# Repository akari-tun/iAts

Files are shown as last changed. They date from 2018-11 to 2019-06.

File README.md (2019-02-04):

# iAts
A antenna tracker system for UAV.

## 项目介绍
Arduino自动跟踪云台
蓝牙版AAT

用于装载定向高增益图传天线，通过图传的音频通道传送飞机的坐标位置与高度，再根据本地位置与高度计算出需要指向的方向与俯仰角度，从而将自动将天线指向飞机，不需要人肉调整天线角度，更加专注于飞行与享受FPV的过程。

大部分代码基本来源于开源项目 amv-open360tracker_RX_v1_user 项目地址 https://github.com/raul-ortega/amv-open360tracker/  
修改了以下功能：
1. 修改了程序流程
2. 开发了手机APP进行调参与监控（通过蓝牙连接）
3. 增加了HC05蓝牙模块与手机连接，通过手机APP进行调参
4. 与手机APP通讯，将飞机位置数据通过APP传到手机（使用自定义TLV格式的协议）
5. 手机APP上显示飞机的位置

## APP

[iAts_app](https://github.com/akari-tun/iAts_app) 可以对云台进行调参与跟踪飞机位置。

发布版本：
[release v1.0.0-perview](https://github.com/akari-tun/iAts_app/releases/download/1.0.0-perview/iAts_app_V1.0.0-perview.apk)
## 特点

- 低成本，基于328p芯片运行，可以直接使用[MWC MultiWii SE v2.6](https://s.taobao.com/search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)飞控板，或是使用[Arduino Pro Mini](https://store.arduino.cc/usa/arduino-pro-mini)+[HMC5883模块](https://s.taobao.com/search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)/[QMC5883模块](https://s.taobao.com/search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)+[MPU6050模块](https://s.taobao.com/search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)进行构建。
- 云台的运动使用舵机驱动，水平方向使用360°舵机，俯仰方向使用180°或90°舵机，低成本的舵机可以使用[MG995](https://item.taobao.com/item.htm?spm=a230r.1.14.20.24c52706K8ff73&id=45136514387&ns=1&abbucket=11#detail)，它有360°版本与180°版本。
- [OLED](https://item.taobao.com/item.htm?spm=a1z10.5-c-s.w4002-15846751795.28.57594e5cFUP7UZ&id=524527857468)屏幕显示数据，可以显示飞机坐标，速度，GPS星数，本地位置，方向等数据。
- 开发了手机APP进行调参与监控，可以在APP的地图中显示飞机的位置。
- 发射端可以支持NMEA协议与MAVLink协议，输出标准的LTM协议与地面端通信。
- 使用图传的音频通道传输数据到地面端，地面端与发射端都使用[TCM3105芯片](https://s.taobao.com/search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)进行数模转换。
- 云台旋转部分与底座需要使用[微型滑环](https://s.taobao.com/search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)，防止绕线。
- 使用卡尔曼滤波算法融合加速度计与指南针数据，减少指南针漂移引起的抖动。
- 地面端使用了MOZ8上djzoom大佬设计的PCB，原帖：[让每个人都能用起的舵机版AAT](http://www.moz8.com/forum.php?mod=viewthread&tid=83868&highlight=%E8%88%B5%E6%9C%BA%2BAAT&_dsign=e2235060)
- 发射端让同事帮忙画了新的PCB。
- AAT通过蓝牙连接手机，通过手机获取本地GPS位置，省略了“设置家”的步骤或是“本地GPS模块”。
  
## 成品展示

#### 硬件电路部

##### 接收端原理图
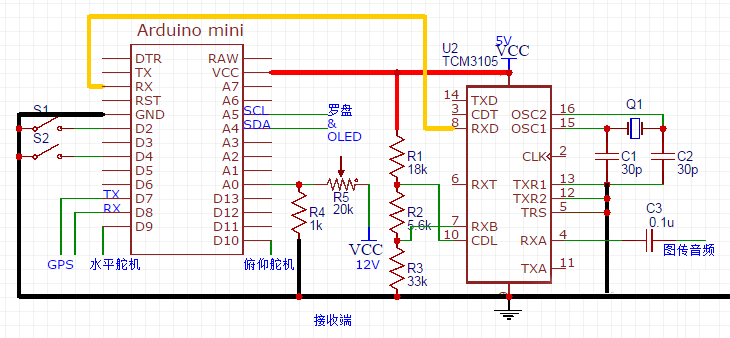
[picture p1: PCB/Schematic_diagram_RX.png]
Schematic_diagram_RX

  
##### 发射端原理图
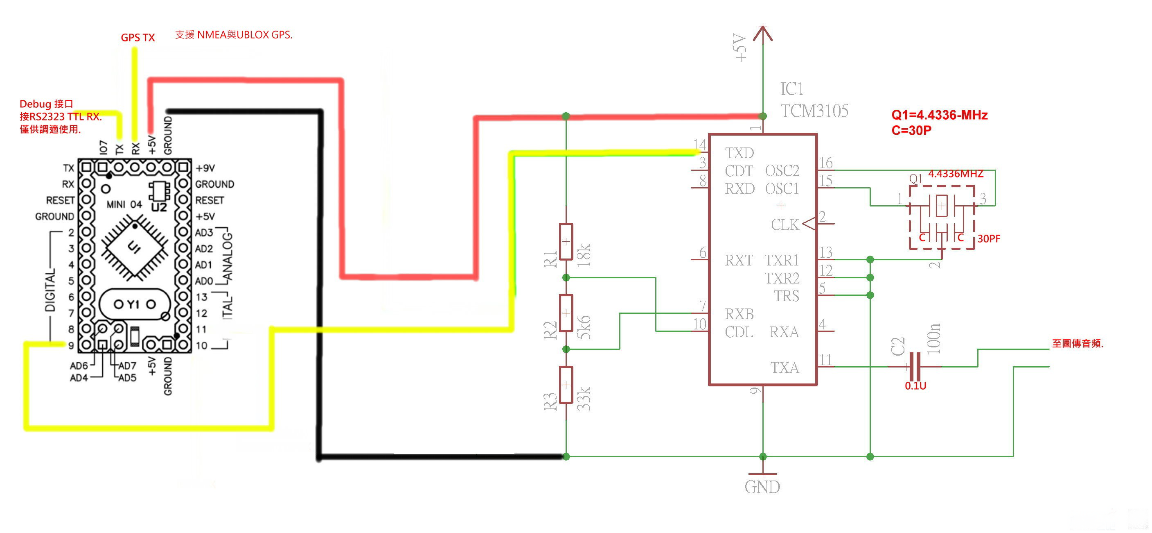
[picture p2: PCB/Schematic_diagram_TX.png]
Schematic_diagram_TX

  
##### 打样回来的PCB
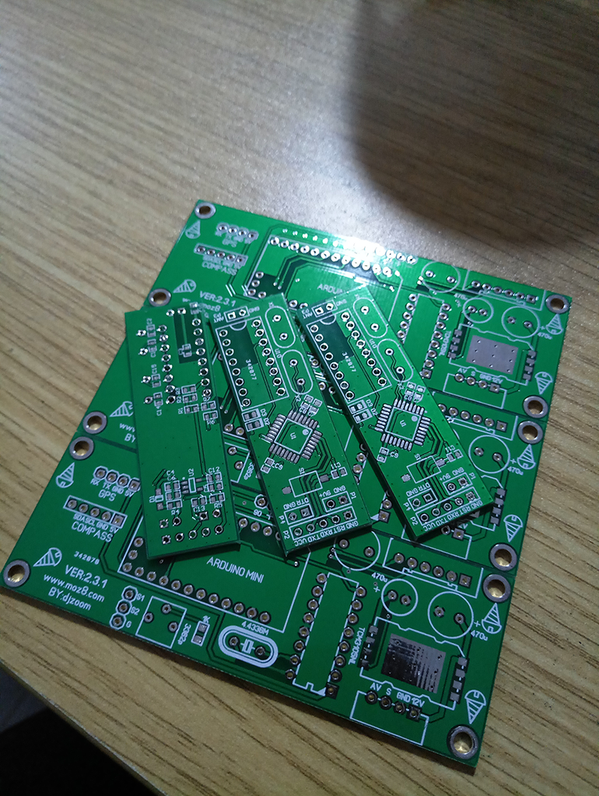
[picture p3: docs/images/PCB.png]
PCB

  
##### 发射机
焊好的发射端，由于使用5V供电，所以电源部分可以不需要焊了

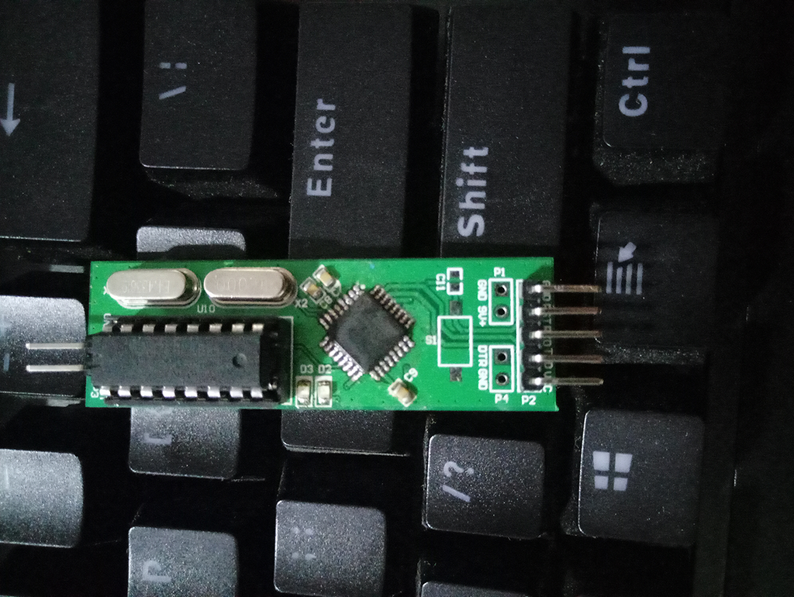
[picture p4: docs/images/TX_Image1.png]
TX


#### 前面板

前面板包含以下几个部分：
- 3个LED灯
  红色接收到图传信号并解析成功数据开始闪烁，蓝色在手机蓝牙连接成功并向手机发送数据闪烁，绿色在接收到手机发送的数据闪烁。
- 12V电源插口
  用于给图传接收机供电。
- AUX音视频插口 
  用于连接图传接收机，传输视频与音频信号，视频信号通过滑环穿过底座接显示屏，音频信号通过TCM3105芯片转换为数字信号。
- OLED屏幕
  显示GPS坐标，速度，方向，云台指向，云台电压，本地GPS坐标，高度等数据。
  
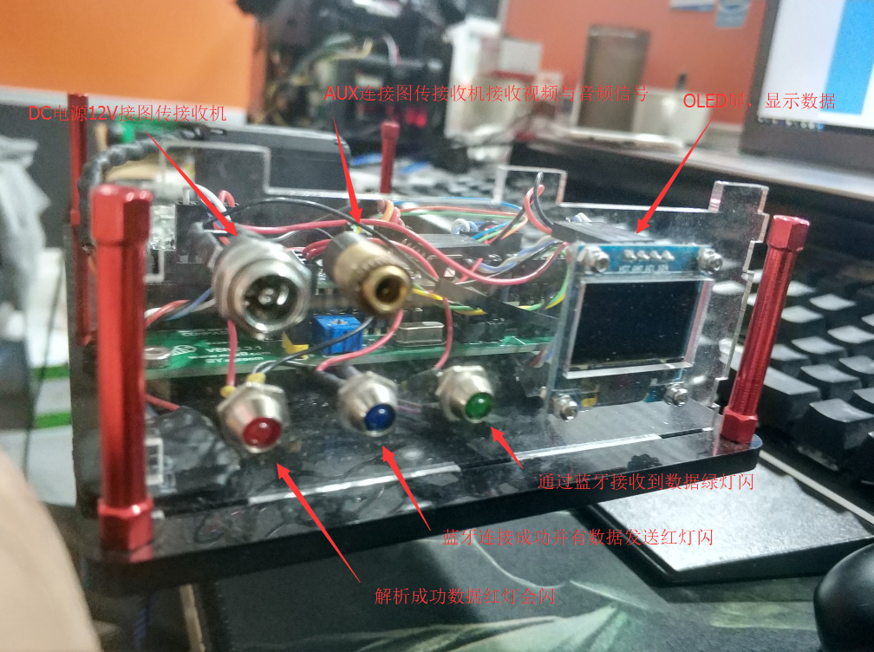
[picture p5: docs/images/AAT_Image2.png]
 

#### 内部细节

##### MPU6050模块
MPU6050用于测量水平旋转的加速度，使用卡尔曼滤波算法融合测量的指南针数据进行计算，消除指南针数据的漂移。

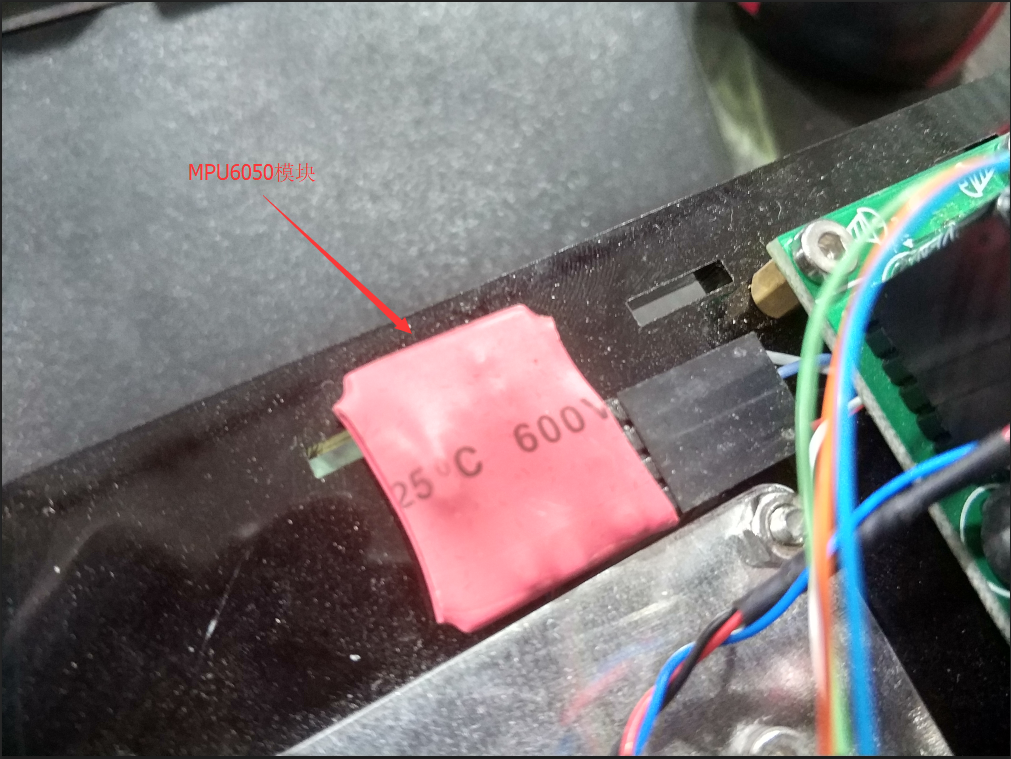
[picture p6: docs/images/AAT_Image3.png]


##### HMC5883L模块
HMC5883L磁力计用于测量指向的角度，通过融合MPU6050的加速度数据进行卡尔曼滤波来消除漂移。

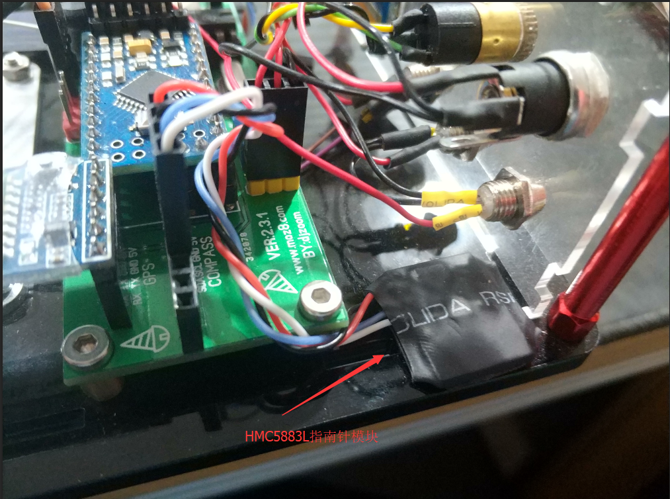
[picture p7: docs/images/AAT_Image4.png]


##### 微型滑环
平台与底座使用滑环导电，通过滑环可以防止360°旋转的时候将导线缠绕。

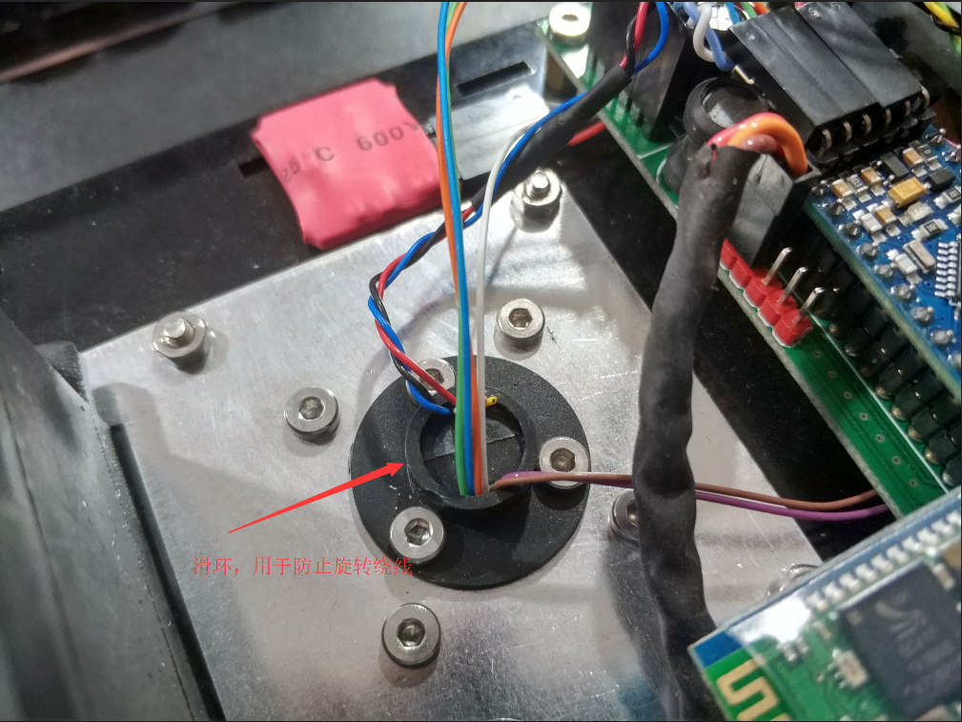
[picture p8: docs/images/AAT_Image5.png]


##### HC05蓝牙模块
蓝牙模块用于与手机蓝牙连接

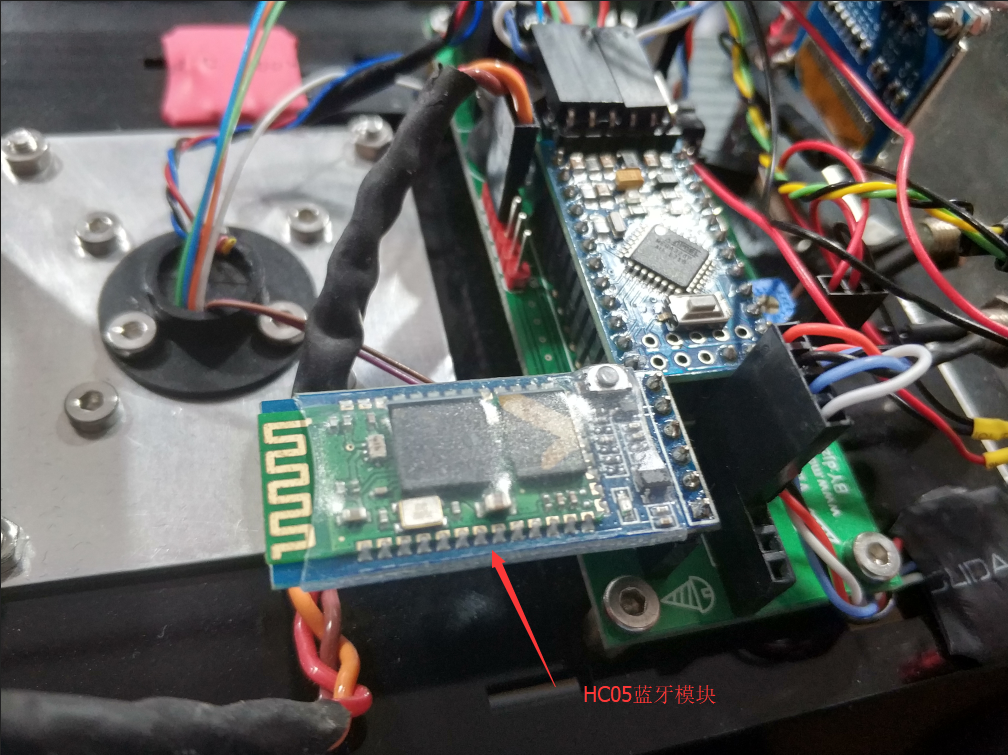
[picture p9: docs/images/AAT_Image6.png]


##### 接收板
接收板上焊接了Arduino Pro Mini模块，开关电源模块，TCM3105芯片，供电分做量部分，通过滑环进来的12V电源，一部分通过开关电源模块降压到5V给两个舵机供电，好处是支持电流大，效率高，但是纹波比较大，所以后部有滤波电容，另一部分通过LM7805电源芯片降压到5V给Pro Mini供电。

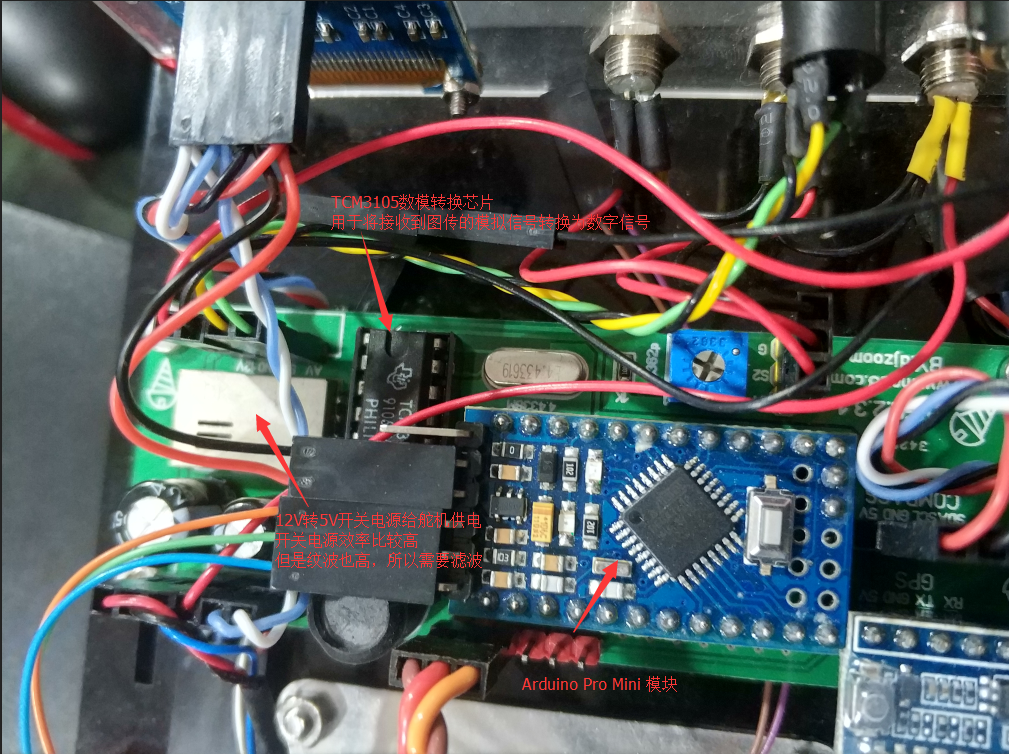
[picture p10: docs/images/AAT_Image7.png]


##### 水平360°舵机
水平舵机提供360°的旋转支持。

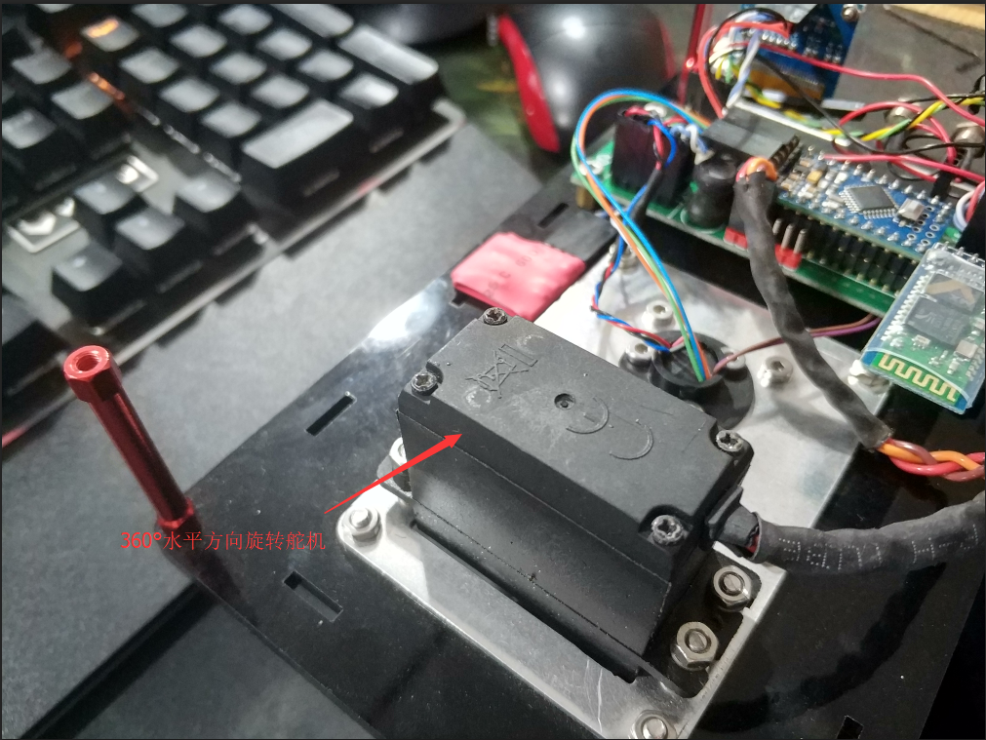
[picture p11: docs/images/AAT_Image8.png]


##### 内部整体图

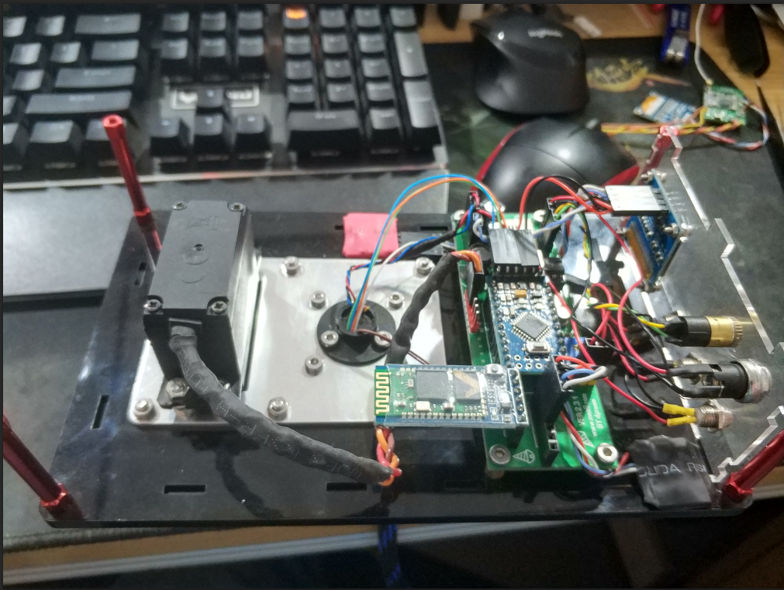
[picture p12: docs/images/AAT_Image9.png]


#### 外部细节

##### 底座
底座机械部分由djzoom群里的大佬设计加工，我购买的成品，底座上的齿轮固定，通过水平舵机上的齿轮旋转带动云台水平转动，底座内有两个轴承支撑平台，滑环的线通过轴承中心穿出底座，由于底座使用了CNC加工，虽然坚固漂亮，但是成本较高。

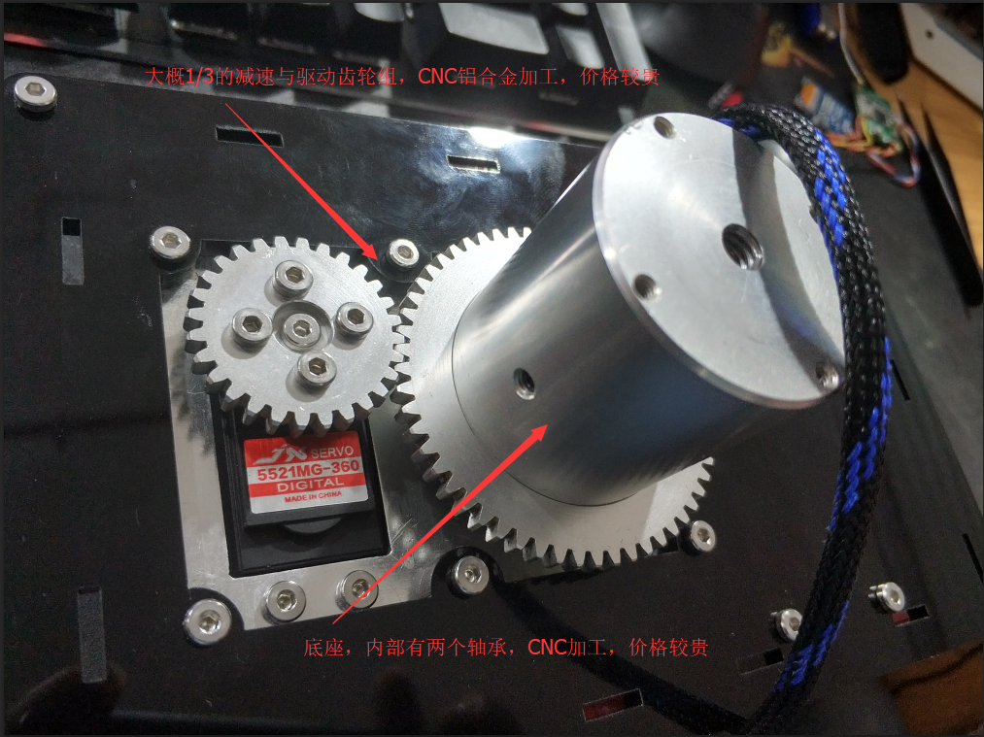
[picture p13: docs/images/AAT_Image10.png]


##### 1/4英寸螺孔
底部提供了标准的1/4英寸螺孔，可以直接安装到普通的相机三脚架上。

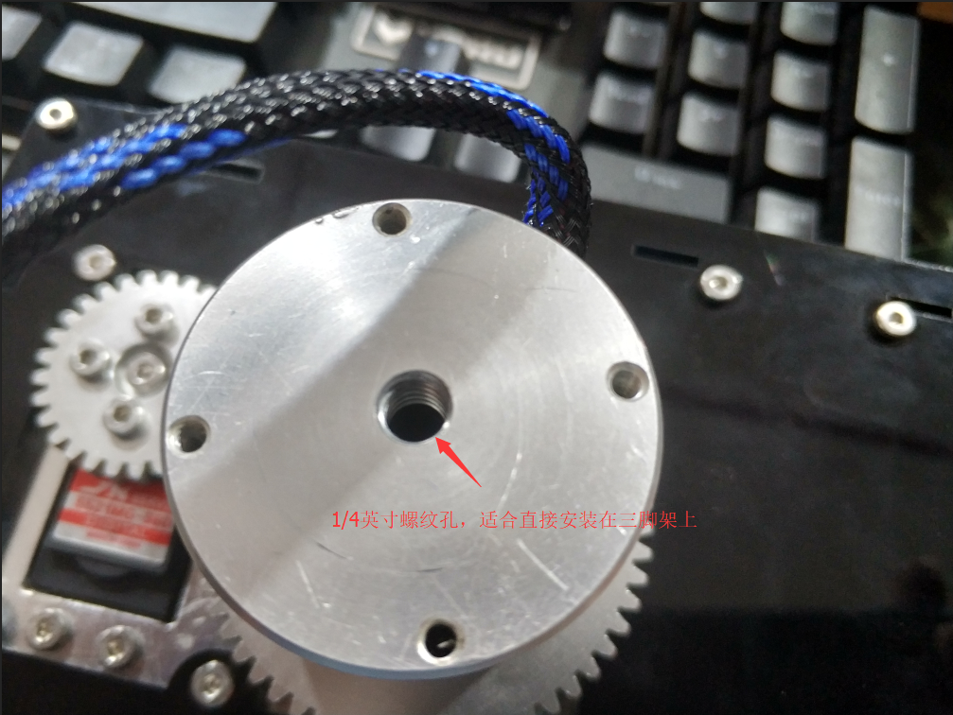
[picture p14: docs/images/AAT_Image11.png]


##### 外部整体图
外壳使用了5mm黑色亚克力加工了上盖板与下盖板，上下盖板间使用了40mm铝柱支撑固定,俯仰固定安装在上盖板上，使用了舵机配送的摇臂来安装天线支架，天线支架使用1/4英寸手拧螺丝来安装[枫叶23db大平板](https://item.taobao.com/item.htm?spm=a1z10.5-c.w4002-10110629054.23.3cf95b54f4w6pb&id=543939433629)，图传接收机使用了开源的双接收，用3D打印的外壳，直接用双面胶粘在盖板上，另外把水平尺也装在了盖板上，用于使用时调平。

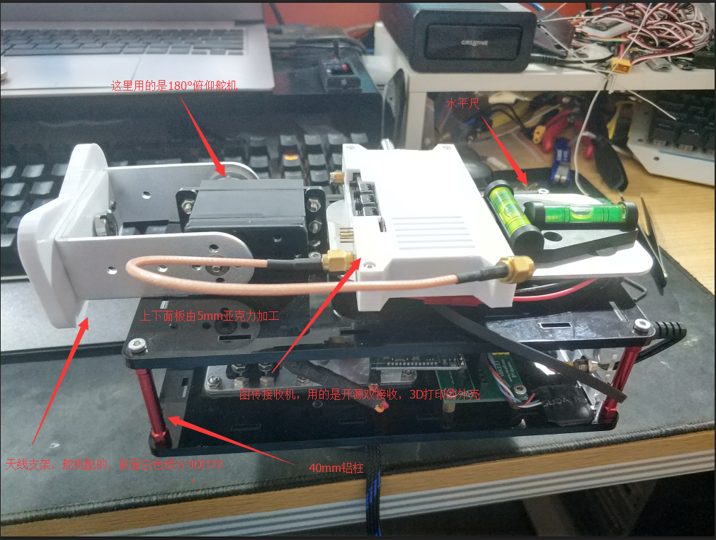
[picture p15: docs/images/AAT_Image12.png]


#### 外场使用

##### 整体图
正在测试的成品，用的是枫叶大平板，由于比较重，有点抖。

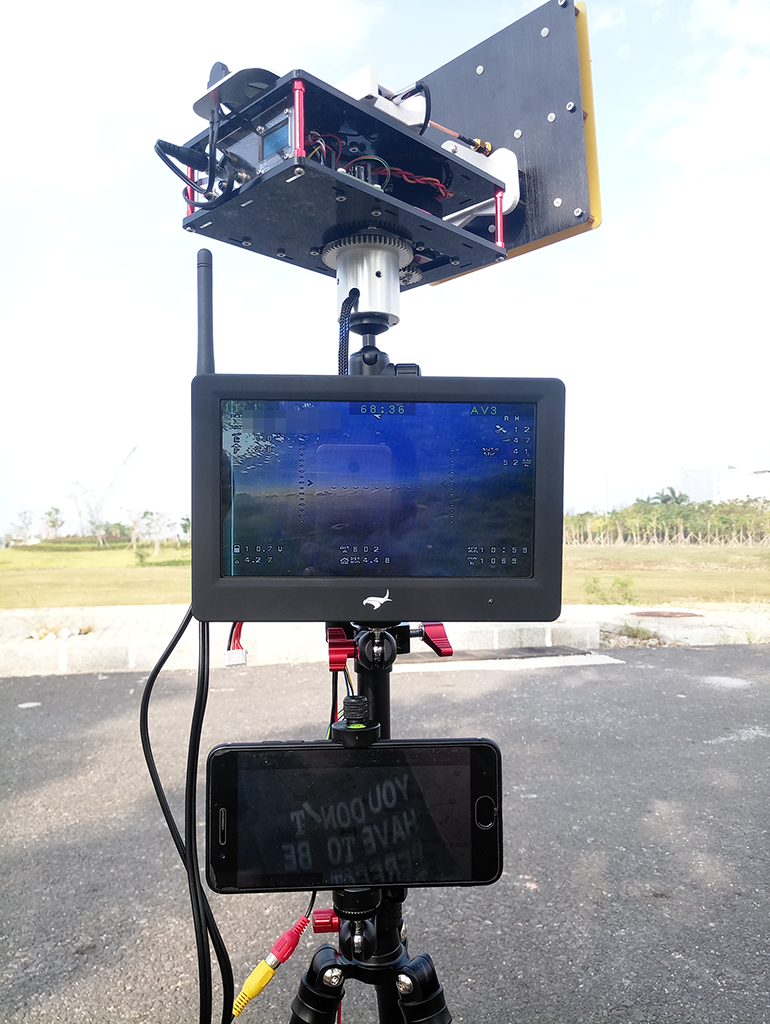
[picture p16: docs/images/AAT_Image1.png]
成品


##### APP截图
APP跟踪界面截图，可以看到飞机位置，经纬度，高度，距离，速度，AAT的电压，指向角度，俯仰角度

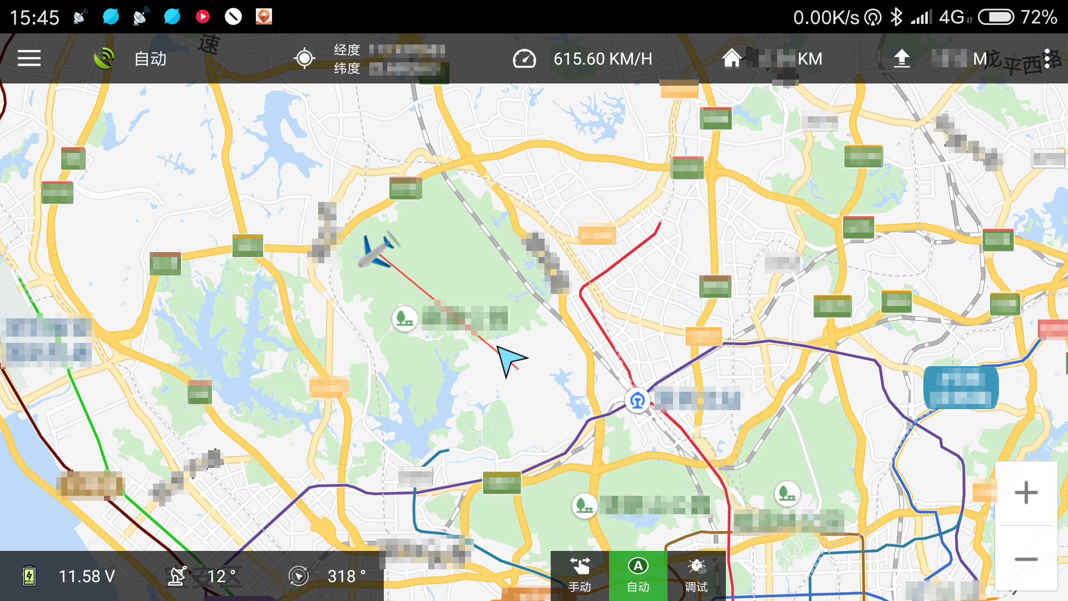
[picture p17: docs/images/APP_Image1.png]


调参界面
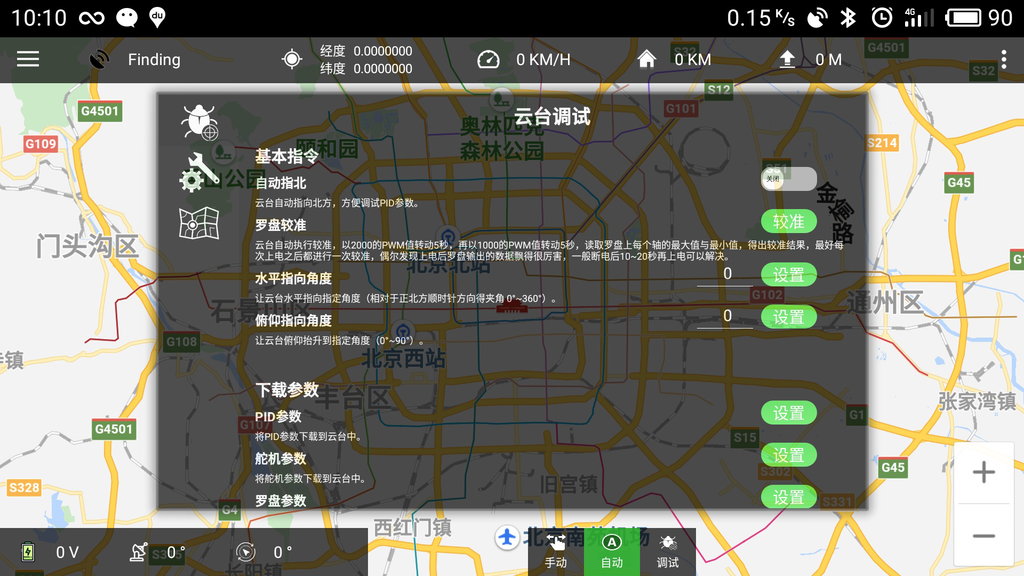
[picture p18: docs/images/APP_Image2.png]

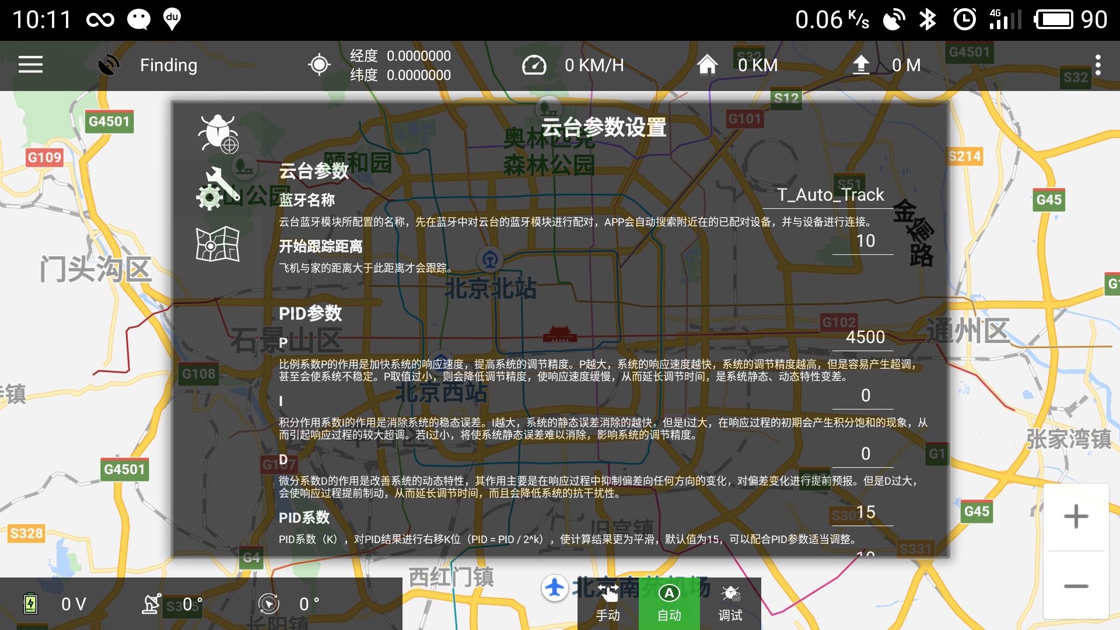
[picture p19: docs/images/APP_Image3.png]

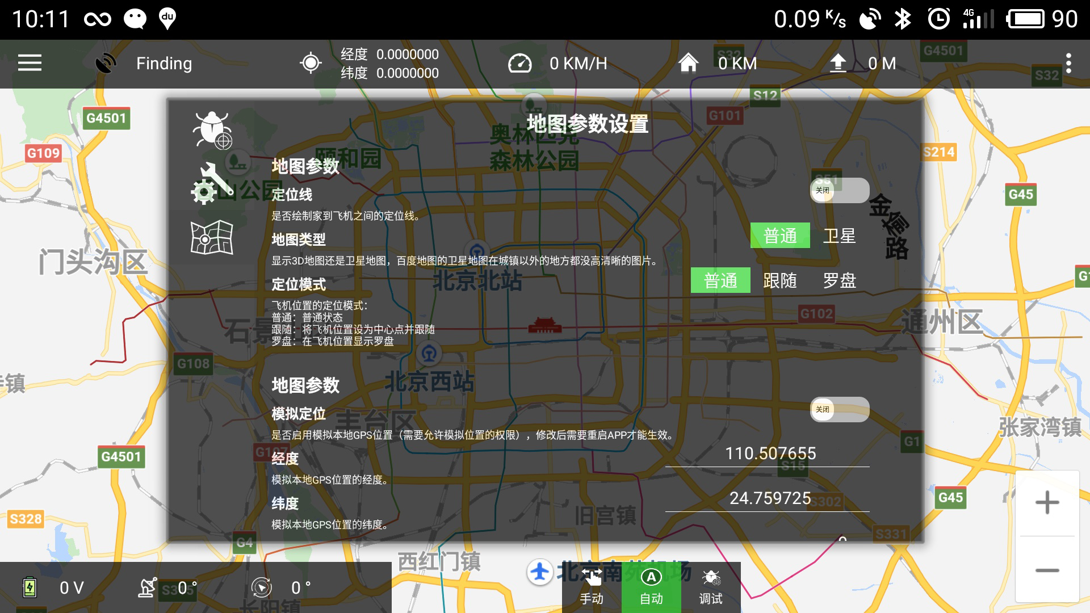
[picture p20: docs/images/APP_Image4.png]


#### 视频：<Br/>
- [模拟测试](https://www.bilibili.com/video/av31897946/) <Br/>
- [上飞机实测](https://www.bilibili.com/video/av33431415/)

## 安装教程

正在撰写。。。

## 使用说明

正在撰写。。。

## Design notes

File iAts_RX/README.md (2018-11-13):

# T_Auto_Tracker

#### 项目介绍
Arduino自动跟踪云台
蓝牙版AAT

#### 软件架构
大部分代码基本来源于开源项目 amv-open360tracker_RX_v1_user 项目地址 https://github.com/raul-ortega/amv-open360tracker/  

修改了以下功能：
1. 重写了loop()函数
1. 蓝牙调参，蓝牙上传数 
2. 蓝牙传输GPS数据，在手机上显示飞机位置  
3. 修改了一点点发射端与接收端的通讯协议，传输了更多的数据  
4. 优化PID算法，加入变积分过程  
5. 加入国产QMC5883芯片的支持  
6. 加入MPU6050并使用卡尔曼滤波，消除指南针漂移
  
针对此固件的APP正在开发中。。。

#### 安装教程

1. xxxx
2. xxxx
3. xxxx

#### 使用说明

1. xxxx
2. xxxx
3. xxxx

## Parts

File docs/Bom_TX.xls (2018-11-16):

BOM
类型 | Comment | 数量 | 位号 | 封装
IC | TCM3105 | 1 | U1 | DIP16
 | ME6219 | 1 | U2 | LC-SOT-23-5
 | ATmaga328P-AU | 1 | U1 | TQFP80P900X900X120_HS-32N
电容 | 30pF/0603/5% | 4 | C1, C2,C14,C15 | C0603
 | 0.1uF/50V/10% | 7 | C3, C4, C7, C8, C9, C10, C13 | C0603
 | 2.2uF/50V/10% | 2 | C5, C11 | C0603
 | 10uF/10V/10%钽电容 | 2 | C6, C12 | A型
电阻 | 100R/5%/0603 | 3 | R4, R6, R7 | R0603
 | 5K6/5%/0603 | 1 | R2 | R0603
 | 10K/5%/0603 | 1 | R5 | R0603
 | 18K/5%/0603 | 1 | R1 | R0603
 | 33K/5%/0603 | 1 | R3 | R0603
晶振 | 4.4336MHz | 1 | X1 | LC-HC-49S
 | 12Mhz | 1 | X2 | LC-HC-49S
二极管、LED | 1N4148 | 1 | D1 | SOD123
 | 蓝色LED | 1 | D2 | D0603
 | 红色LED | 1 | D3 | D0603
排针 | 2pin2.54mm间距排针 | 2 | P1, P3 | HDR1X2
 | 5pin2.54mm间距排针 | 1 | P2 | HDR1X5
按键 | SW-PB | 1 | S1 | Buttle_SMD

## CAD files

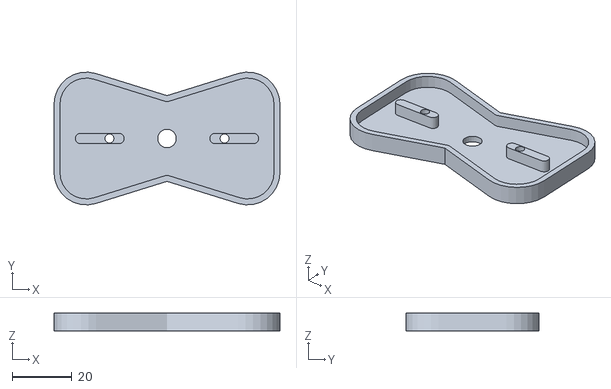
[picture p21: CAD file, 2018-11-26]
docs/cases/Antenna_Holder_2.stl
75.6 x 44.4 x 6.00

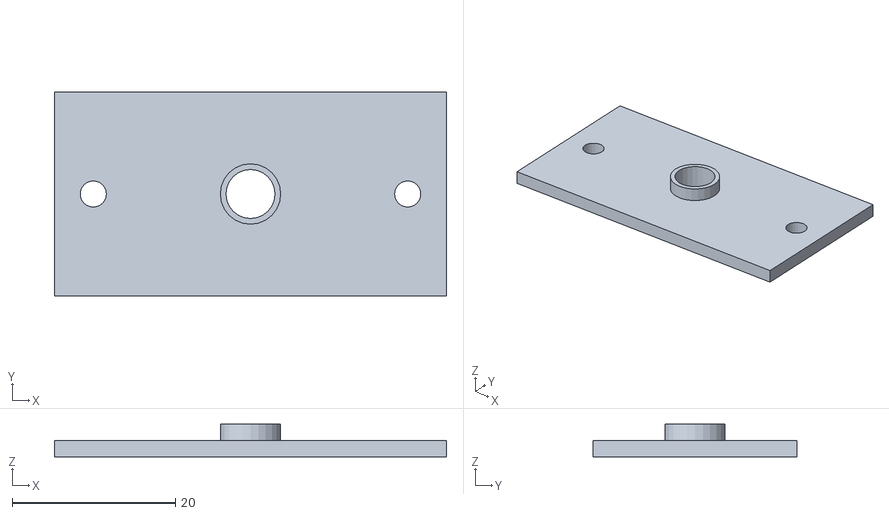
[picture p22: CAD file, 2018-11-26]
docs/cases/Antenna_Holder_1.stl
48.0 x 25.0 x 4.00

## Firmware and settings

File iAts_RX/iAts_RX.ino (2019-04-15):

/*
作者：TanJun
用途：蓝牙版AAT

部分代码来源于开源项目 amv-open360tracker_RX_v1_user 项目地址 https://github.com/raul-ortega/amv-open360tracker/
在此基础上做了一些修改
1.重新构建主流程，使执行过程更合理
2.蓝牙调参，蓝牙上传数
3.蓝牙传输GPS数据，在手机上显示飞机位置
4.加入了PID变积分算法，使之能更快的修正误差
*/

#include <Arduino.h>
#include <Wire.h>			  //I2C
#include <SSD1306Ascii.h>	  //OLED屏
#include <SSD1306AsciiWire.h> //OLED屏
#include <SoftwareSerial.h>   //软串口
#include "defines.h"		  //基础定义
#include "config.h"			  //配置定义
#include "telemetry.h"		  //通讯解析
#include "tprotocol.h"		  //协议
#include "battery.h"		  //电压测量
#include "IMU.h"		  	  //惯性测量单元
#include "servos.h"			  //舵机控制
#include "calc.h"			  //计算数据

SoftwareSerial digitalSerial(T_GPS_RX_PIN, T_GPS_TX_PIN);
SSD1306AsciiWire oled;
IMU imu;

char oled_str[24];

struct Airplane airplane;
struct Tracker tracker;
struct Parameter TParam;

long Error[11];
long Accumulator;
long PID;
// double AccGain;
int16_t _servo_tilt_must_move = -1;

int softserial_delay = (int)round(10000000.0f / (DIGITAL_SERIAL_BAUDRATE)); // time to wait between each byte sent.

// uint16_t last_course;
// unsigned long airplane_pos_time;
unsigned long airplane_upload_time;
unsigned long tracker_upload_time;
unsigned long heart_upload_time;
unsigned long compass_time;
unsigned long oled_time;

boolean is_bt_conn;

uint8_t *p_send_data;
uint8_t send_len;
uint8_t send_index;
uint32_t frame_timer;

void getError();
void calculatePID();
boolean sendToBluetooth();
void calcTilt();

void setup()
{
	pinMode(VOLTAGEDIVIDER, INPUT);
	pinMode(LED_DIGITAL_PIN, OUTPUT);
	pinMode(LED_SERIAL_PIN, OUTPUT);
	pinMode(LED_ENCODE_PIN, OUTPUT);
	pinMode(EN_33V_PIN, OUTPUT);

	/* 激活3.3V稳压模块 */
	digitalWrite(EN_33V_PIN, HIGH);
	delay(100);

	/* 初始化一些变量 */
	tracker.mode = 1;
	p_send_data = 0;
	send_len = 0;
	send_index = 0;
	airplane_upload_time = 0;
	tracker_upload_time = 0;
	heart_upload_time = 0;
	compass_time = 0;
	oled_time = 0;
	SERVO_TILT_HAS_ARRIVED = true;
	//AccGain = 0;

	//测试代码初始化
	// tracker.mode = 1;
	// TParam.pid_p = 6000;
	// TParam.pid_i = 50;
	// TParam.pid_d = 200;
	// TParam.pid_divider = 15;
	// TParam.pid_max_error = 40;
	// TParam.tilt_min = 1100;
	// TParam.tilt_max = 2150;
	// TParam.pan_center = 1505;
	// TParam.pan_min_speed = 50;
	// TParam.compass_offset = 180;
	// TParam.compass_declination = 0;
	// TParam.start_tracking_distance = 10;
	/* ------------------------------------------ */

	//设置参考电压为默认值
	analogReference(BATTERYMONITORING_VREF_SOURCE);

	/* OLED屏初始化 */
	Wire.begin();
	oled.begin(&Adafruit128x64, OLED_I2C_ADDRESS);
	oled.set400kHz();
	oled.setFont(font8x8);
	oled.println("T Auto Tracker");
	oled.println("Version 1.0.0");
	oled.println("    ");
	delay(1000);
	/* ------------------------------------------ */

	HAS_ALT = false;
	HAS_FIX = false;
	HOME_SETED = false;
	BT_CONNECTED = false;
	BT_DATA_SENDING = false;

	/* 初始化电子指南针 */
	Wire.setClock(uint32_t(400000L));
	Wire.begin();
	oled.println("IMU Init...");
	imu.init();
	/* ------------------------------------------ */

	/* 初始化传输协议 */
	oled.println("Protocol Init...");
	tprotocol(&airplane, &tracker, &TParam);
	telemetry(&airplane);
	/* ------------------------------------------ */

	/* 初始化传输协议 */
	oled.println("Servos Init...");
	//initServos(&tracker_param);
	initServos(&TParam);
	/* ------------------------------------------ */

	/* 软串口--接收AD转换后的数字信号 */
	digitalSerial.begin(DIGITAL_SERIAL_BAUDRATE);
	/* ------------------------------------------ */

	/* 物理串口--链接蓝牙模块 */
	Serial.begin(PHYSICAL_SERIAL_BAUDRATE);
	/* ------------------------------------------ */

	TParam.pid_divider = 15;
	// airplane_pos_time = millis();
	airplane_upload_time = millis();
	tracker_upload_time = millis() + 500;
	heart_upload_time = millis();
	compass_time = millis();
	oled_time = millis();
}

void loop()
{
	//int8_t i;

	digitalWrite(LED_DIGITAL_PIN, LOW);
	digitalWrite(LED_ENCODE_PIN, LOW);
	digitalWrite(LED_SERIAL_PIN, LOW);

	//if (Serial.available())
	if (digitalSerial.available())
	{
		//uint8_t c = Serial.read();
		uint8_t c = digitalSerial.read();
		//digitalSerial.write(c);

		if (encodeTargetData(c) && HAS_ALT && HAS_FIX) digitalWrite(LED_DIGITAL_PIN, HIGH);

		digitalWrite(LED_DIGITAL_PIN, HIGH);

		// else if (tracker.mode == TRACKER_MODE_DEBUG)
		// {
		// 	//target heading in degree
		// 	if (c == 'H' || c == 'h') tracker.course = Serial.parseInt();
		// 	else if (c == 'T' || c == 't')
		// 	{
		// 		//tilt angle in degree
		// 		int value = Serial.parseInt();
		// 		if (value > 90) value = 90;
		// 		else if (value < 0)	value = 0;

		// 		oled.clear();
		// 		sprintf(oled_str, "Tilt set to:%03u", value);
		// 		oled.println(oled_str);

		// 		_servo_tilt_must_move = value;
		// 		SERVO_TILT_HAS_ARRIVED = false;
		// 	}
		// 	else if (c == 'M' || c == 'm')
		// 	{
		// 		//tilt angle in ms
		// 		tracker.pitching = Serial.parseInt();
		// 		SET_TILT_SERVO_SPEED(tracker.pitching);
		// 	}
		// 	else if (c == 'L' || c == 'l') TParam.pan_center = Serial.parseInt();
		// 	else if (c == 'P' || c == 'p') TParam.pid_p = Serial.parseInt();
		// 	else if (c == 'I' || c == 'i') TParam.pid_i = Serial.parseInt();
		// 	else if (c == 'D' || c == 'd') TParam.pid_d = Serial.parseInt();
		// 	else if (c == 'C' || c == 'c') calibrate_compass(TParam.pan_center);
		// 	else if (c == 'S' || c == 's') TParam.pan_min_speed = Serial.parseInt();
		// 	else if (c == 'O' || c == 'o') TParam.compass_offset = Serial.parseInt();
		// 	else if (c == 'E' || c == 'e') TParam.pid_max_error = Serial.parseInt();
		// 	else if (c == 'G' || c == 'g') TRACKING_STARTED = Serial.parseInt();
		// 	else if (c == 'W' || c == 'w') tracker.outpwm = Serial.parseInt();

		// 	digitalWrite(LED_DIGITAL_PIN, HIGH);
		// }
	}

	//if (digitalSerial.available())
	if (Serial.available())
	{
		//uint8_t c = digitalSerial.read();
		uint8_t c = Serial.read();
		if (encodeTrackerData(c))
			digitalWrite(LED_ENCODE_PIN, HIGH);
	}

	//根据当前的模式处理对应的数据
	switch (tracker.mode)
	{
		case TRACKER_MODE_MANUAL:
			break;
		case TRACKER_MODE_AUTO:
			//Only track if home is seted.
			if (HAS_FIX && HOME_SETED)
			{
				airplane.distance = distance_between(tracker.lat / 10000000.0f, tracker.lon / 10000000.0f,
													airplane.lat / 10000000.0f, airplane.lon / 10000000.0f);
				tracker.course = course_to(tracker.lat / 10000000.0f, tracker.lon / 10000000.0f,
										airplane.lat / 10000000.0f, airplane.lon / 10000000.0f) *
								10.0f;

				HAS_FIX = false;

				//Only track if tracking process started.
				if (!TRACKING_STARTED)
				{
					//if plane is START_TRACKING_DISTANCE meter away from tracker start tracking process.
					if (airplane.distance >= TParam.start_tracking_distance)
						TRACKING_STARTED = true;
				}

				// unsigned long dt = (millis() - airplane_pos_time);

				// if (dt > 0) {
				// 	uint16_t er = abs(tracker.course - last_course);

				// 	if (er > 1800) er = 3600 - er;

				// 	AccGain = (er / (dt / 100.0)) * 1.1;

				// 	last_course = tracker.course;
				// 	airplane_pos_time = millis();
				// }
			}

			if (SERVO_TILT_HAS_ARRIVED && HAS_ALT && TRACKING_STARTED && airplane.distance < 120000 && airplane.alt < 500000)
			{
				calcTilt();
				tracker.pitching = _servo_tilt_must_move;
				HAS_ALT = false;

				// if(_servo_tilt_must_move > 88) 
				// {
				// 	Serial.print("T LAT:");
				// 	dtostrf(airplane.lat / 10000000.0f, 10, 5, oled_str);
				// 	Serial.println(oled_str);
				// 	Serial.print("T LON:");
				// 	dtostrf(airplane.lon / 10000000.0f, 10, 5, oled_str);
				// 	Serial.println(oled_str);
				// 	sprintf(oled_str, "PLAN_ALT:%05d  DST:%05u", (int)(airplane.alt / 100.0f), airplane.distance);
				// 	Serial.println(oled_str);
				// 	sprintf(oled_str, "TKER_ALT:%05u  S:%05u", (int)(tracker.alt / 100.0f), airplane.speed);
				// 	Serial.println(oled_str);
				// }
			}
			break;
		case TRACKER_MODE_DEBUG:
			if (TRACKING_STARTED) TRACKING_STARTED = false;
			//处理下发下来要执行的命令
			uint8_t cmd = getReceiveCmd();

			if (cmd != 0)
			{
				switch (cmd)
				{
					case TAG_CTR_CALIBRATE:
						oled.clear();
						oled.setCursor(0, 0);
						oled.println("Calibrating");
						imu.calibrate_compass(TParam.pan_center);
						oled.clear();
						break;
					case TAG_CTR_MODE:
						oled.clear();
						break;
					case TAG_CTR_TILT:
						_servo_tilt_must_move = tracker.pitching;
						SERVO_TILT_HAS_ARRIVED = false;
						#ifdef DEBUG
							Serial.print("CTR_TILT:");
							Serial.println(_servo_tilt_must_move);
						#endif
						break;
				}
			}
			break;
	}

	// only update pan value if there is new data
	if ((TRACKING_STARTED || AUTO_POINT_TO_NORTH) && NEW_HEADING)
	{
		getError();		// Get position error
		calculatePID(); // Calculate the PID output from the error
		NEW_HEADING = false;
	}

	SET_PAN_SERVO_SPEED(tracker.outpwm);
	servo_tilt_update(_servo_tilt_must_move);

	// refresh rate of compass is 75Hz -> 13.333ms to refresh the data
	// we update the heading every 14ms to get as many samples into the smooth array as possible
	if (millis() > compass_time)
	{
		compass_time = millis() + 14;

		// double heading = (imu.getHeading() * 10) + TParam.compass_declination - (TParam.compass_offset) * 10;

		// if (heading < 0)
		// 	tracker.heading = (uint16_t)(3600 + heading);
		// else
		// 	tracker.heading = (uint16_t)heading;

		double heading = imu.getHeading();
		if (heading < 0) heading += 360;

		int16_t tmp = (heading * 10) + TParam.compass_declination + (TParam.compass_offset * 10);
		if (tmp < 0) tmp += 3600;
		tracker.heading = (uint16_t)tmp;

		NEW_HEADING = true;
	}

	// 通过蓝牙上报飞机状态
	if (BT_CONNECTED && millis() > airplane_upload_time)
	{
		airplane_upload_time = millis() + 500;
		setSendCmd(CMD_U_AIRPLANE);
	}

	// 通过蓝牙上报设备状态
	if (BT_CONNECTED && millis() > tracker_upload_time)
	{
		tracker_upload_time = millis() + 500;
		setSendCmd(CMD_U_TRACKER);
	}

	if (millis() > heart_upload_time)
	{
		heart_upload_time = millis() + 25000;
		setSendCmd(CMD_U_HEARTBEAT);

		if (millis() > getLastHeartBeetAck() + 30000)
			BT_CONNECTED = false;
	}

	//获取需要发送的数据
	if (send_index <= 0)
	{
		getSendData(p_send_data, send_len);
		send_index = send_len;
	}

	if (send_index > 0)
	{
		//发送数据
		if (sendToBluetooth())
			digitalWrite(LED_SERIAL_PIN, HIGH);
	}

	if (millis() > oled_time)
	{
		long t = millis() - oled_time;

		getBatVoltage(&tracker.voltage);

		if (tracker.mode == TRACKER_MODE_DEBUG)
		{
			oled.setCursor(0, 0);
			sprintf(oled_str, "H:%03u A:%03u", tracker.heading / 10, tracker.course / 10);
			oled.println(oled_str);
			sprintf(oled_str, "PWM:%04d PID:%03d", tracker.outpwm, PID);
			oled.println(oled_str);
			sprintf(oled_str, "T0:%04u T90:%04u", TParam.tilt_0, TParam.tilt_90);
			oled.println(oled_str);
			sprintf(oled_str, "C:%04d E:%03u", TParam.pan_center, TParam.pid_max_error);
			oled.println(oled_str);
			sprintf(oled_str, "O:%03d    V:%02u.%02u", TParam.compass_offset, tracker.voltage / 100, tracker.voltage % ((uint16_t)(tracker.voltage / 100) * 100));
			oled.println(oled_str);
			sprintf(oled_str, "P:%04d         ", TParam.pid_p);
			oled.println(oled_str);
			sprintf(oled_str, "I:%04d         ", TParam.pid_i);
			oled.println(oled_str);
			sprintf(oled_str, "D:%04d         ", TParam.pid_d);
			oled.println(oled_str);
		}
		else if (tracker.mode == TRACKER_MODE_AUTO)
		{
			oled.setCursor(0, 0);
			sprintf(oled_str, "H:%03u A:%03u S:%02u", tracker.heading / 10, tracker.course / 10, airplane.sats);
			oled.println(oled_str);
			sprintf(oled_str, "A:%05d  D:%05u", (int)(airplane.alt / 100.0f), airplane.distance);
			oled.println(oled_str);
			oled.print("T LAT:");
			dtostrf(airplane.lat / 10000000.0f, 10, 5, oled_str);
			oled.println(oled_str);
			oled.print("T LON:");
			dtostrf(airplane.lon / 10000000.0f, 10, 5, oled_str);
			oled.println(oled_str);
			//sprintf(oled_str, "V:%02u.%02u  T:%05u", tracker.voltage / 100, tracker.voltage % ((uint16_t)(tracker.voltage / 100) * 100), t);
			sprintf(oled_str, "V:%02u.%02u  H:%05u", tracker.voltage / 100, tracker.voltage % ((uint16_t)(tracker.voltage / 100) * 100), airplane.heading);
			oled.println(oled_str);
			sprintf(oled_str, "A:%05u  S:%05u", (int)(tracker.alt / 100.0f), airplane.speed);
			oled.println(oled_str);
			oled.print("L LAT:");
			dtostrf(tracker.lat / 10000000.0f, 10, 5, oled_str);
			oled.println(oled_str);
			oled.print("L LON:");
			dtostrf(tracker.lon / 10000000.0f, 10, 5, oled_str);
			oled.println(oled_str);
		}

		oled_time = millis() + 500;
	}
}

/*
	将数据发送到蓝牙
*/
boolean sendToBluetooth()
{
	boolean byte_dropped = false;
	boolean packet_dropped = false;

	if (send_index == send_len) frame_timer = millis();

	// for (i = 0; i < send_len; i++)
	// {
	// Serial.print(p_send_data[send_len - send_index], HEX);
	//Serial.print(" ");
	//if (digitalSerial.write(p_send_data[send_len - send_index]) == 0)
	if (Serial.write(p_send_data[send_len - send_index]) == 0)
	{
		//buffer is full, flush & retry.
		Serial.flush();
		byte_dropped = true;
		if (millis() - frame_timer >= 100)
		{
			// drop the whole frame, it's too old. Will resend a fresh one.
			packet_dropped = true;
			// break;
		}
	}
	else
	{
		send_index -= 1;
	}

	if (byte_dropped)
	{
		// i--; //resend dropped byte
		byte_dropped = false;
	}
	if (packet_dropped)
	{
		BT_DATA_SENDING = false;
		send_index = 0;
		// break;
	}

	// int32_t currentmicros = micros();
	// while ((micros() - currentmicros) < softserial_delay );// wait at least 1 byte is sent
	// }

	//Serial.println("");
	return !packet_dropped;
}

//////////////// Me he quedado aquí revisando los #ifdef
//Tilt angle alpha = atan(alt/dist)
void calcTilt()
{
	uint16_t alpha = 0;

	//this will fix an error where the tracker randomly points up when plane is lower than tracker
	if (airplane.alt < tracker.alt)
	{
		airplane.alt = tracker.alt;
	}

	//prevent division by 0
	if (airplane.distance == 0)
	{
		// in larger altitude 1m distance shouldnt mess up the calculation.
		//e.g. in 100m height and dist 1 the angle is 89.4° which is actually accurate enough
		airplane.distance = 1;
	}

	alpha = toDeg(atan((airplane.alt / 100.00f - tracker.alt / 100.00f) / airplane.distance));

	//just for current tests, later we will have negative tilt as well
	if (alpha < 0)
		alpha = 0;
	else if (alpha > 90)
		alpha = 90;

	_servo_tilt_must_move = alpha;
	SERVO_TILT_HAS_ARRIVED = false;
	//moveServoTilt(alpha);
	// SET_TILT_SERVO_SPEED(map(alpha, 0, 90, TParam.titl_0, TParam.titl_90));
}

void getError(void)
{
	int16_t delta = tracker.course - tracker.heading;

	// Serial.println("-----------Error[11]------------");
	// Serial.print("[0]");Serial.print(delta);
	// shift error values
	for (byte i = 0; i < 10; i++)
	{
		Error[i + 1] = Error[i];
		// Serial.print(" [");Serial.print(i + 1);Serial.print("]");Serial.print(Error[i + 1]);
	}
	// Serial.println("");
	// Serial.println("------------------");

	if (delta > 1800)
	{
		delta -= 3600;
	}
	else if (delta < -1800)
	{
		delta += 3600;
	}
	// load new error into top array spot
	Error[0] = delta;
}

void calculatePID(void)
{
	float index;

	//变积分过程
	if (abs(Error[0]) > 300)
	{ 
		index = 0.0;
	}
	else if (abs(Error[0]) < 50)
	{
		index = 1.0;
		Accumulator += Error[0];
	}
	else
	{
		index = (300 - abs(Error[0])) / 300;
		Accumulator += Error[0];
	}

	PID = TParam.pid_p * Error[0] + index * TParam.pid_i * Accumulator + TParam.pid_d * (Error[0] - Error[10]);
	PID = PID >> TParam.pid_divider;

	if (PID >= 500)
		PID = 500;
	if (PID <= -500)
		PID = -500;

	if (Error[0] > TParam.pid_max_error)
	{
		tracker.outpwm = TParam.pan_center + PID + TParam.pan_min_speed;
	}
	else if (Error[0] < -1 * TParam.pid_max_error)
	{
		tracker.outpwm = TParam.pan_center + PID - TParam.pan_min_speed;
	}
	else
	{
		tracker.outpwm = TParam.pan_center;
	}
}

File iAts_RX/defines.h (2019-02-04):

#ifndef DEFINES_H
#define DEFINES_H

#include <inttypes.h>
#include "config.h"

#define OLED_I2C_ADDRESS    0x3C

#define T_GPS_RX_PIN        8
#define T_GPS_TX_PIN        7
#define VOLTAGEDIVIDER      A0
#define LED_DIGITAL_PIN     13
#define LED_SERIAL_PIN      2
#define LED_ENCODE_PIN      4
#define EN_33V_PIN          6

#define PARAM_EPPROM_POS  	6
#define PARAM_EPPROM_POS_PID_P  	              PARAM_EPPROM_POS + 0
#define PARAM_EPPROM_POS_PID_I  	              PARAM_EPPROM_POS + 2
#define PARAM_EPPROM_POS_PID_D  	              PARAM_EPPROM_POS + 4
#define PARAM_EPPROM_POS_PID_DIVIDER  	        PARAM_EPPROM_POS + 5
#define PARAM_EPPROM_POS_PID_MAX_ERROR 	        PARAM_EPPROM_POS + 6
#define PARAM_EPPROM_POS_TILT_0  	              PARAM_EPPROM_POS + 8
#define PARAM_EPPROM_POS_TILT_90   	            PARAM_EPPROM_POS + 10
#define PARAM_EPPROM_POS_PAN_CENTER  	          PARAM_EPPROM_POS + 12
#define PARAM_EPPROM_POS_PAN_MIN_SPEED 	        PARAM_EPPROM_POS + 14
#define PARAM_EPPROM_POS_COMPASS_OFFSET	        PARAM_EPPROM_POS + 15
#define PARAM_EPPROM_POS_COMPASS_DECLINATION  	PARAM_EPPROM_POS + 17
#define PARAM_EPPROM_POS_START_TRACKING_DISTANCE  	PARAM_EPPROM_POS + 18

#define TRACKER_MODE_MANUAL 0
#define TRACKER_MODE_AUTO   1
#define TRACKER_MODE_DEBUG  2

//lat and lon required in units of millionths of a degree -> precision of 5 digits after '.'
// for example 52.52081 -> 5252081
//             13.40945 -> 1340945
struct Airplane
{
  // latitude in units of millionths of a degree
  uint32_t lat;
  // longitude in units of millionths of a degree
  uint32_t lon;
  // altitude ranging from -32.768m to 32.767m
  uint32_t alt;
  // pitch in 0-359° *10
  uint16_t pitch;
  // roll in 0-359° *10
  uint16_t roll;
  // heading in 0-359° *10
  uint16_t heading;
  // distance from 0 ... 64km
  uint16_t distance;
  // speed 0-255
  uint16_t speed;
  // sats
  uint8_t sats;
  // fix_type
  uint8_t fix_type;
};

struct Tracker
{
  uint32_t lat;         //纬度
  uint32_t lon;         //经度
  uint32_t alt;         //高度
  uint16_t heading;     //朝向
  uint8_t pitching;     //俯仰
  uint16_t voltage;     //电压
  uint8_t mode;         //跟踪模式
  uint16_t course;		//飞机指向
  uint16_t outpwm;		//输出脉冲
  int8_t declination;	//本地磁偏角
};

struct Parameter
{
	uint16_t pid_p;
	uint16_t pid_i;
	uint16_t pid_d;
  uint8_t pid_divider;
  uint8_t pid_max_error;
	uint16_t tilt_0;
	uint16_t tilt_90;
	uint16_t pan_center;
  uint8_t pan_min_speed;
	int16_t compass_offset;
  int8_t compass_declination;
	uint8_t start_tracking_distance;
};

//typedef struct
//{
//	uint16_t pid_p;
//	uint16_t pid_i;
//	uint16_t pid_d;
//	uint16_t titl_0;
//	uint16_t titl_90;
//	uint16_t pan_0;
//	uint8_t compass_offset;
//	uint8_t start_tracking_distance;
//	uint8_t max_pid_error;
//	uint8_t max_pan_speed;
//	uint8_t min_pan_speed;
//} TrackerTParameter;
//
//TrackerTParameter *TParam;

//#define PID_P						((volatile TrackerTParameter *)(&TParam))->pid_p
//#define PID_I						((volatile TrackerTParameter *)(&TParam))->pid_i
//#define PID_D						((volatile TrackerTParameter *)(&TParam))->pid_d
//#define TITL_0						((volatile TrackerTParameter *)(&TParam))->titl_0
//#define TITL_90						((volatile TrackerTParameter *)(&TParam))->titl_90
//#define PAN_0						((volatile TrackerTParameter *)(&TParam))->pan_0
//#define COMPASS_OFFSET				((volatile TrackerTParameter *)(&TParam))->compass_offset
//#define START_TRACKING_DISTANCE		((volatile TrackerTParameter *)(&TParam))->start_tracking_distance
//#define MAX_PID_ERROR				((volatile TrackerTParameter *)(&TParam))->max_pid_error
//#define MAX_PAN_SPEED				((volatile TrackerTParameter *)(&TParam))->max_pan_speed
//#define MIN_PAN_SPEED				((volatile TrackerTParameter *)(&TParam))->min_pan_speed

typedef struct
{
  bool f0 : 1;
  bool f1 : 1;
  bool f2 : 1;
  bool f3 : 1;
  bool f4 : 1;
  bool f5 : 1;
  bool f6 : 1;
  bool f7 : 1;
} PackedBool;

#define HOME_SETED		   ((volatile PackedBool *)(&GPIOR0))->f0
#define TRACKING_STARTED ((volatile PackedBool *)(&GPIOR0))->f1
#define CURRENT_STATE    ((volatile PackedBool *)(&GPIOR0))->f2
#define PREVIOUS_STATE   ((volatile PackedBool *)(&GPIOR0))->f3
#define HAS_FIX          ((volatile PackedBool *)(&GPIOR0))->f4
#define HAS_ALT          ((volatile PackedBool *)(&GPIOR0))->f5
#define BT_CONNECTED		 ((volatile PackedBool *)(&GPIOR0))->f6
#define NEW_HEADING      ((volatile PackedBool *)(&GPIOR0))->f7

typedef struct
{
	bool f0 : 1;
	bool f1 : 1;
	bool f2 : 1;
	bool f3 : 1;
	bool f4 : 1;
	bool f5 : 1;
	bool f6 : 1;
	bool f7 : 1;
} Status;


#define BT_DATA_SENDING			    ((volatile Status *)(&GPIOR1))->f0
#define AUTO_POINT_TO_NORTH			((volatile Status *)(&GPIOR1))->f2
#define SERVO_TILT_HAS_ARRIVED  ((volatile Status *)(&GPIOR1))->f3

#define toRad(val) val * PI/180.0f
#define toDeg(val) val * 180.0f/PI

#define meter2feet(value) value * 3.2808399
#define feet2meter(value) value * 0.3048

#endif

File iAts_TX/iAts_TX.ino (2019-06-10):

/*
iAts_TX is a AAT transmit progam, its from GhettoProxy on https://github.com/KipK/Ghettostation/tree/master/GhettoProxy
I rewrote the code that parses the GPS data and sends the LTM protocol.

作者：TanJun
用途：AAT transmit for iAts

*/

#include <FastSerial.h>
#include <avr/pgmspace.h>
#include <Arduino.h>
#include <AP_Math.h>
#include <Metro.h>
#include <AltSoftSerial.h>

#include "Config.h"
#include "Defines.h"
#include "iAts_TX.h"
#include "LightTelemetry.cpp"
#ifdef DEBUG
#include <MemoryFree.h>
#endif
/*
 * BOF preprocessor bug prevent
 */
#define nop() __asm volatile("nop")
#if 1
nop();
#endif
/*
 * EOF preprocessor bug prevent
*/

#ifdef PROTOCOL_MAVLINK
#include <AP_Common.h>
#include <GCS_MAVLink.h>
#include "Mavlink.cpp"
#define MAVLINK_CRC_EXTRA 0
#endif
#ifdef PROTOCOL_NMEA
#include "GPS_NMEA.cpp"
#include "GPS.cpp"
#endif

//################################### SETTING OBJECTS ###############################################

//##### LOOP RATES
Metro loop10hz = Metro(100); //10hz loop
Metro loop50hz = Metro(20); //10hz loop
#ifdef DEBUG
Metro loopDebug = Metro(500);
#endif
//#################################### SETUP LOOP ####################################################

bool gps_ready = false;
bool isSending = false;
bool led = false;

void setup()
{
  //start serial com
  init_serial();
#ifdef PROTOCOL_GPS
  GPS.Init();
#endif
#ifdef PROTOCOL_MAVLINK
  mavlink_comm_0_port = &Serial;
#endif

  pinMode(LED_GPS_PIN, OUTPUT);
  pinMode(LED_OUT_PIN, OUTPUT);
  //LED off
  digitalWrite(LED_GPS_PIN, LOW);
  digitalWrite(LED_OUT_PIN, LOW);

  gps_ready = false;
}

//######################################## MAIN LOOP #####################################################################
void loop()
{
  if (get_telemetry() && !gps_ready) gps_ready = true;

  //LED Controller
  if (loop50hz.check()) {
    if (led && (gps_ready || isSending)) digitalWrite(LED_GPS_PIN, HIGH);
    else digitalWrite(LED_GPS_PIN, LOW);

    led = !led;
  }

#ifdef DEBUG
  if (loopDebug.check())
  {
    debug_proxy();
  }
#endif

#ifdef ONE_BYTE_PARSE_AND_SEND
  if (send()) {
    isSending = false;
    if (loop10hz.check() && gps_ready) {
      LTM();
      gps_ready = false;
      isSending = true;
      frame_timer = millis();
    }
  }
#else
  if (loop10hz.check() && gps_ready) {
    LTM();
    gps_ready = false;
    frame_timer = millis();
    while (!send()) { }
  }
#endif
}

//######################################## TELEMETRY FUNCTIONS #############################################
void init_serial()
{
  Serial.begin(INPUT_BAUD);
  SerialPort2.begin(OUTPUT_BAUD);
}

//Preparing adding other protocol
bool get_telemetry()
{

#if defined(PROTOCOL_MAVLINK) // Ardupilot / PixHawk / Taulabs ( mavlink output ) / Other
  if (enable_frame_request == 1)
  { //Request rate control
    enable_frame_request = 0;
    if (!PASSIVEMODE)
    {
      request_mavlink_rates();
    }
  }

  read_mavlink();

  if (uav_fix_type >= 0x02) gps_ready = true;
#endif

#if defined(PROTOCOL_NMEA) || defined(PROTOCOL_UBLOX)
  return gps_read();
#endif
}

#ifdef DEBUG

void debug_proxy()
{
  //SerialPort1.print("timer ");
  //int currenttime = millis();
  //SerialPort1.println(currenttime);
  Serial.print("mem ");
  int freememory = freeMem();
  Serial.println(freememory);
  Serial.print("uav_alt = ");
  Serial.println(uav_alt);
  Serial.print("uav_pitch = ");
  Serial.println(uav_pitch);
  Serial.print("uav_roll = ");
  Serial.println(uav_roll);
  Serial.print("uav_heading = ");
  Serial.println(uav_heading);
  Serial.print("uav_lat = ");
  Serial.println(uav_lat);
  Serial.print("uav_lon = ");
  Serial.println(uav_lon);
  Serial.print("uav_speed = ");
  Serial.println(uav_groundspeed);
  Serial.print("uav_fix_type = ");
  Serial.println(uav_fix_type);
  Serial.print("uav_satellites_visible = ");
  Serial.println(uav_satellites_visible);
  //SerialPort1.print("softserial_delay = ");
  //SerialPort1.println(softserial_delay);
  //SerialPort1.print("packet_drops = ");
  //SerialPort1.println(packet_drops);
  //SerialPort1.print("parse_error = ");
  //SerialPort1.println(parse_error);
}
#endif

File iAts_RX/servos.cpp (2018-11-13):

#include "calc.h"
#include "servos.h"

float _lasttilt = 0.0;
uint8_t _tilt_pos = 0;
static Parameter *PTParam;

// Initializes both hardware PWMs to be used for tilt and pan servos.
//void initServos()
void initServos(Parameter *param)
{
	PTParam = param;
	// Set OC1A (PB1) and OC1B (PB2) to output.
	// these are our hardware PWM ports.

	DDRB |= _BV(PORTB1) | _BV(PORTB2);

	// Setup of Timer1, Prescaler 8, 16bit fast pwm
	TCCR1A = _BV(WGM11) | _BV(COM1A1) | _BV(COM1B1);
	TCCR1B = _BV(WGM12) | _BV(WGM13) | _BV(CS11);
	// we need to multiply our pwm value by 2
	OCR1A = PTParam->pan_center * 2;
	OCR1B = PTParam->tilt_0 * 2;
	//OCR1A = PAN_0 * 2;
	//OCR1B = TITL_0 * 2;
	// ((16mhz / 8 Prescaler) / 50hz) - 1 = 40000
	ICR1 = 39999;
}

void moveServoTilt(float value)
{
	int _pwmpulse;
	float easingout;
	if (abs(_lasttilt - value) > TILT_EASING_MIN_ANGLE)
	{
		for (int pos = 0; pos < TILT_EASING_STEPS; pos++)
		{
			if (_lasttilt <= value)
				easingout = _lasttilt + easeTilt(pos, 0, value - _lasttilt, TILT_EASING_STEPS);
			else
				easingout = _lasttilt - easeTilt(pos, 0, _lasttilt - value, TILT_EASING_STEPS);
			_pwmpulse = (int)map(easingout, 0, 90, PTParam->tilt_0, PTParam->tilt_90);
			//_pwmpulse = (int)map(easingout, 0, 90, TITL_0, TITL_90);
			SET_TILT_SERVO_SPEED(_pwmpulse);
			delay(15);
		}
	}
	else
		SET_TILT_SERVO_SPEED(map(value, 0, 90, PTParam->tilt_0, PTParam->tilt_90));
		//SET_TILT_SERVO_SPEED(map(value, 0, 90, TITL_0, TITL_90));
	_lasttilt = (float)value;
}

void servo_tilt_update(int16_t &_servo_tilt_must_move)
{
	int _pwmpulse;
	float easingout;
	if (_servo_tilt_must_move < 0)
		_tilt_pos = 0;
	if (!SERVO_TILT_HAS_ARRIVED && _servo_tilt_must_move > -1)
	{
		if (abs(_lasttilt - _servo_tilt_must_move) > TILT_EASING_MIN_ANGLE)
		{
			if (_tilt_pos < TILT_EASING_STEPS)
			{
				if (_lasttilt <= _servo_tilt_must_move)
					easingout = _lasttilt + easeTilt(_tilt_pos, 0, _servo_tilt_must_move - _lasttilt, TILT_EASING_STEPS);
				else
					easingout = _lasttilt - easeTilt(_tilt_pos, 0, _lasttilt - _servo_tilt_must_move, TILT_EASING_STEPS);
				_pwmpulse = (int)map(easingout, 0, 90, PTParam->tilt_0, PTParam->tilt_90);
				//_pwmpulse = (int)map(easingout, 0, 90, TITL_0, TITL_90);
				SET_TILT_SERVO_SPEED(_pwmpulse);

#if TILT_EASING_MILIS
				delay(TILT_EASING_MILIS);
#endif
				_tilt_pos++;
			}
			else
			{
				if (_tilt_pos == TILT_EASING_STEPS)
				{
					SET_TILT_SERVO_SPEED(map(_servo_tilt_must_move, 0, 90, PTParam->tilt_0, PTParam->tilt_90));
					//SET_TILT_SERVO_SPEED(map(_servo_tilt_must_move, 0, 90, TITL_0, TITL_90));
#if TILT_EASING_MILIS
					delay(TILT_EASING_MILIS);
#endif
					_lasttilt = (float)_servo_tilt_must_move;
					_tilt_pos = 0;
					SERVO_TILT_HAS_ARRIVED = true;
					_servo_tilt_must_move = -1;
				}
			}
		}
		else
		{
			SERVO_TILT_HAS_ARRIVED = true;
			_servo_tilt_must_move = -1;
		}
	}
}

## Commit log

2018-11-16 Add RX and TX pcb to repository.
2018-11-16 Add schematic diagram and TX bom.
    [Bom_TX.xls]
2018-11-17 Add TX bom.
    [Bom_TX.xls]
2018-11-17 Add some cases.
    [Antenna_Holder_1.stl, Antenna_Holder_2.stl]
2018-12-03 Update TX pcb.
2018-12-03 Add case.
2019-02-04 修复Mavlink协议解析Heading的问题
2019-04-15 fix upload debug version to github.
    [config.h, iAts_RX.ino]
